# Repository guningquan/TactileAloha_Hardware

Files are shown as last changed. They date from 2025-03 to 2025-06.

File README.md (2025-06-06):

# TactileAloha_Hardware
#### Main Project Website: https://guningquan.github.io/TactileAloha

This repository is one of the repositories in the TactileAloha project.  
We organize the code of the TactileAloha project as follows:  

- **This repository** contains the hardware-related code, which is used for launching ROS hardware and should be placed in the ROS workspace.  
- **Another repository,** [TactileAloha_ML](https://github.com/guningquan/act-triple-plus), focuses on robot teleoperation, dataset collection, and imitation learning algorithms. It can be placed anywhere on your computer.

<!-- This repository contains the hardware-related code for the TactileAloha project.  
The TactileAloha project includes two parts: this repository, which focuses on hardware, and another repository related to robot teleoperation, dataset collection, and imitation learning algorithm [TactileAloha_ML](https://github.com/guningquan/act-triple-plus). -->

## 📂 Repo Structure
- **`aloha/`** - Contains core components related to the TactileAloha module, including the TactileAloha launch and the 3D printed model.
- **`digit_interface/`** - An interface for GelSight tactile sensing that can launch and publish GelSight tactile information.
- **`tactile_aloha_monitor/`** - Monitoring tools for TactileAloha.
- **`README.md`** - Project documentation and setup instructions.  

---

## 🏗️ Quick Start Guide

### 🖥️ Software Selection – OS Compatibility

This project has been tested and confirmed to work with the following configuration:  

- ✅ **Ubuntu 20.04 + ROS 1 Noetic** (Fully tested and verified)  

Other configurations may work as well, but they have not been tested yet. If you successfully run this project on a different setup, feel free to contribute by sharing your experience! 🚀

### 🛠️ Software installation - ROS:
1. Install ROS and Interbotix Software: You can install ROS and the Interbotix software by following the official documentation: [Interbotix X-Series Arms Documentation](https://docs.trossenrobotics.com/interbotix_xsarms_docs/). 
Alternatively, you can run the following commands to automate the installation:
    ```sh
    sudo apt install curl
    curl 'https://raw.githubusercontent.com/Interbotix/interbotix_ros_manipulators/main/interbotix_ros_xsarms/install/amd64/xsarm_amd64_install.sh' -o xsarm_amd64_install.sh
    chmod +x xsarm_amd64_install.sh
    ./xsarm_amd64_install.sh -d noetic
    ```
2. This will create the directory ``~/interbotix_ws`` which contains ``src``.
3. Clone our repository inside `~/interbotix_ws/src`， and go to ``~/interbotix_ws/src/interbotix_ros_toolboxes/interbotix_xs_toolbox/interbotix_xs_modules/src/interbotix_xs_modules/arm.py``, find function ``publish_positions``. Change ``self.T_sb = mr.FKinSpace(self.robot_des.M, self.robot_des.Slist, self.joint_commands)`` to ``self.T_sb = None``.
4. ``source /opt/ros/noetic/setup.sh && source ~/interbotix_ws/devel/setup.sh``.
5. ``sudo apt-get install ros-noetic-usb-cam && sudo apt-get install ros-noetic-cv-bridge``.
6. run ``catkin_make`` inside ``~/interbotix_ws``, make sure the build is successful.

### 🧱 Material Preparation
1. Ensure you have the original [ALOHA](https://github.com/tonyzhaozh/aloha) system, which includes at least 4 robots and 3 cameras.
2. Prepare the additional materials required for TactileAloha. The bill of materials, detailing components costing approximately $450 USD beyond the original ALOHA setup, is available [here](https://docs.google.com/spreadsheets/d/1tX9UN2hUqN1ftezxETeFLI59bT0_g0PbhREX1-UMxE8/edit?usp=sharing).
3. 3D print the gripper designed for the tactile sensor. The STL file can be found at aloha/3d_models/gelfinger_v2.stl within this repository.

### 🔧 Hardware Installation
The goal of this section is to run `roslaunch aloha tactile_aloha.launch`, which starts  
communication with **4 robots**, **3 cameras**, and a **Gelsight tactile sensor**.  
Follow these steps to ensure it works properly:

1. We assume you already have the original ALOHA system.

2. `❗` Camera Focus Configuration (Not described in ALOHA):

   The cameras in the ALOHA series are set to **fixed focus** in ROS launch. 
The focus value is configured through `aloha.launch` in `aloha/launch`:  
    ```xml
    <param name="focus" value="40"/>
    ```
   It is necessary to determine the appropriate focus value for each camera; otherwise, the camera image may appear blurry during manipulation.

    The recommended procedure to find a suitable focus value is:
    - To check the available video devices, run the following command: 
   ``` bash
     ls /dev/CAM_*  # or ls /dev/video*
   ```   
    If you have set your camera serial numbers according to [ALOHA](https://github.com/tonyzhaozh/aloha), you can see your camera list as follows:
   ``` bash
     /dev/CAM_HIGH  /dev/CAM_LEFT_WRIST   /dev/CAM_RIGHT_WRIST
   ```  
   
    - Use the following command to open the camera and adjust the focus: 
   ``` bash
     guvcview -d /dev/CAM_HIGH
   ```
    - Test and note the appropriate focus value for each camera ;

3. `❗` Disable Auto Focus:

   - You must disable the continuous autofocus by setting the focus_automatic_continuous control parameter as follows:
    ```bash
      v4l2-ctl -d /dev/CAM_HIGH --set-ctrl focus_automatic_continuous=0
    ```
    - For other cameras please modifiy `/dev/CAM_HIGH` to `/dev/CAM_LEFT_WRIST`, etc.
    - The way to check whether we have set the camera correctly is to run `roslaunch aloha aloha.launch` and ensure that no warning like this appears:
    ```bash
    Error setting controls: Permission denied
    VIDIOC_S_EXT_CTRLS: failed: Permission denied
    ```
   - You can add the following to your `.bashrc`, which allows you to conveniently run `cameras-autofocus` from the command line.
   ```bash
   # Define the cameras-autofocus function to disable autofocus
   cameras-autofocus() {
       # List of camera devices to configure
       cameras=("/dev/CAM_HIGH" "/dev/CAM_LEFT_WRIST" "/dev/CAM_RIGHT_WRIST")
   
       # Function to disable autofocus for a single camera
       disable_autofocus() {
           local camera=$1
           echo "Disabling autofocus for $camera..."
           
           # Disable automatic continuous focus
           v4l2-ctl -d "$camera" --set-ctrl focus_automatic_continuous=0
   
           echo "Autofocus disabled for $camera."
       }
   
       # Main loop to process all cameras
       echo "Configuring autofocus for cameras..."
       for cam in "${cameras[@]}"; do
           if [ -e "$cam" ]; then
               disable_autofocus "$cam"
           else
               echo "Camera $cam not found. Skipping."
           fi
       done
       echo "Autofocus configuration complete."
   }
    ```
   Note: You will need to reapply the focus_automatic_continuous=0 setting whenever you reboot the computer or unplug and replug the cameras.

4. Install the GelSight tactile sensor with the 3D-printed model in the `/aloha/3d_models` directory. We recommend using the [right-angle micro USB cable](https://www.amazon.co.jp/dp/B00ENZDFQ4?ref=ppx_yo2ov_dt_b_fed_asin_title) to connect the sensor with computer, which could reduce collision risk during manipulation. 
Moreover, we install the [noise absorbers](https://www.amazon.co.jp/-/en/gp/product/B0CP491LJR/ref=ewc_pr_img_2?smid=A19BPWQK30Q73P&th=1) for the tactile sensor cable.

5. ⚠️ After installing the tactile sensor, you need to update the `sensor_id` in `tactile_aloha.launch` with a series string like `D20982`.  
In our project, we only utilize one GelSight sensor. If you would like to use multiple GelSight sensors, you can set the `sensor_id` like `D20982_D20983`.  
Meanwhile, you need to use the `setup_digit_multi` function in `digit_interface/scripts/digit.py` along with other corresponding modifications.

6. Install the conda environment for TactileAloha:
    ```sh
    conda create -n aloha python=3.8.10
    conda activate aloha
    pip install -r requirements.txt
    ```
7. You may need to set your aloha conda environment path for `digit.py` in `/digit_interface/scripts/`. For example:
    ```python
    #!/home/ubuntu20/miniforge3/envs/aloha/bin/python
    ```

### ▶️ Testing teleoperation
Before running the commands below, ensure that:  
- **All four robots** are placed in their **sleep positions**.  
- The **master robot's gripper** is **open**.  
    ``` ROS
    # ROS terminal
    conda deactivate
    source /opt/ros/noetic/setup.sh && source ~/interbotix_ws/devel/setup.sh
    roslaunch aloha tactile_aloha.launch
    ```
You can see the three cameras and a real-time GelSight observation on your screen.  
For the teleoperation test, you need to clone the [TactileAloha_ML](https://github.com/guningquan/act-triple-plus) repository and run the command.
The [TactileAloha_ML](https://github.com/guningquan/act-triple-plus) repository can be placed anywhere on your computer; there is no need to place it inside the `interbotix_ws` directory as done in the previous ALOHA series.
   
    # Right hand terminal
    conda activate aloha
    source ~/interbotix_ws/devel/setup.sh
    cd act-triple-plus/aloha_scripts
    python one_side_teleop.py right
    
    # Left hand terminal
    conda activate aloha
    source ~/interbotix_ws/devel/setup.sh
    cd act-triple-plus/aloha_scripts
    python one_side_teleop.py left

The teleoperation will start when the master side gripper is closed.

For more details about teleoperation, dataset collection, data visualization, algorithm training, and development, please refer to the [TactileAloha_ML](https://github.com/guningquan/act-triple-plus) repository.

## 🙏 Acknowledgements
   This project codebase is built based on [ALOHA](https://github.com/tonyzhaozh/aloha) and [ACT](https://github.com/tonyzhaozh/act).

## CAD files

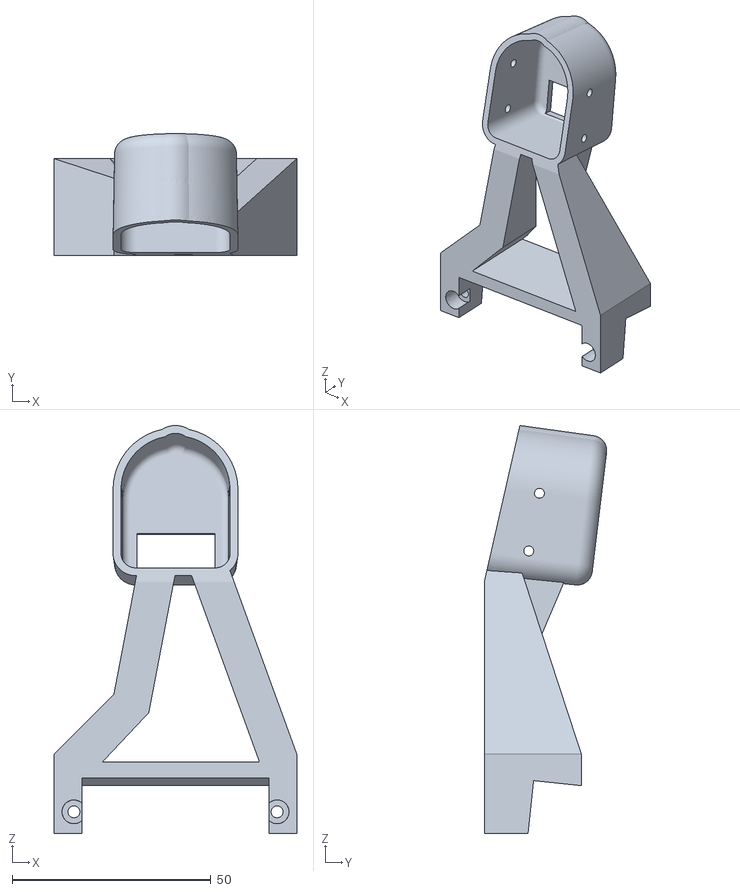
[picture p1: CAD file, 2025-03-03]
aloha/3d_models/gelfinger_v2_mirror.stl
61.0 x 30.8 x 102.6

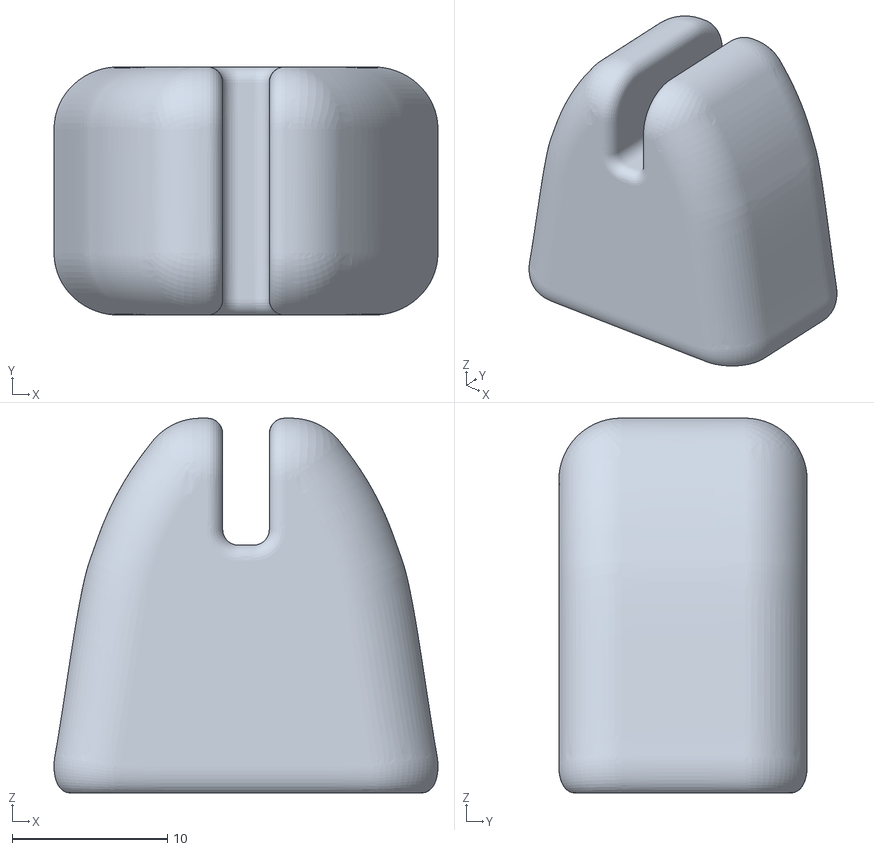
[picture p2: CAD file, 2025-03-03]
aloha/3d_models/support_1.stl
24.7 x 16.0 x 24.1

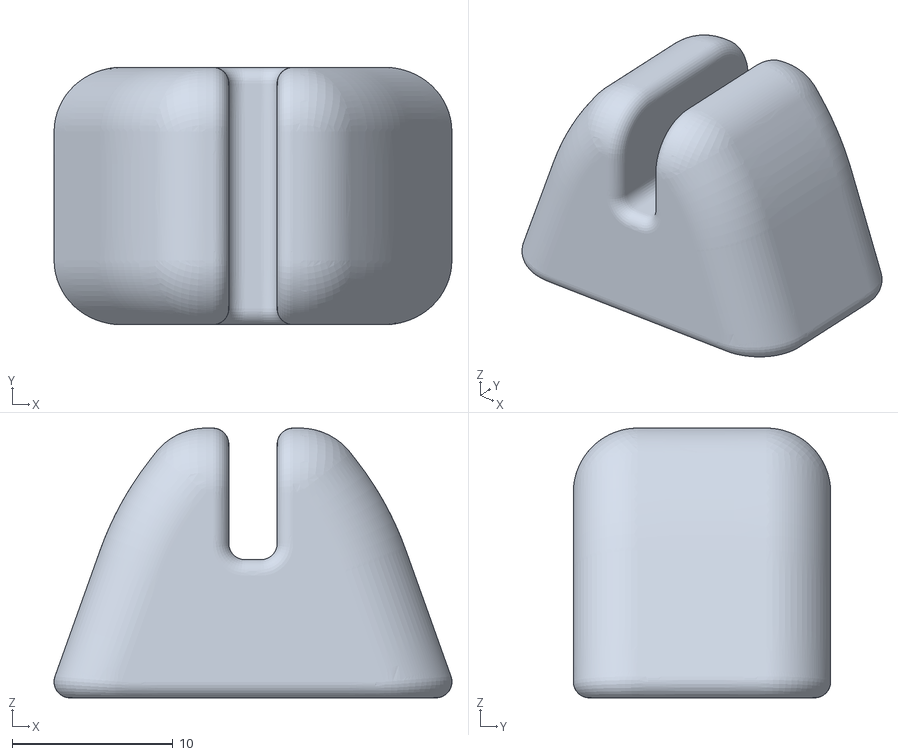
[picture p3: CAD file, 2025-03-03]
aloha/3d_models/support_0.stl
24.7 x 16.0 x 16.8

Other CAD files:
aloha/3d_models/gelfinger_v2.stl
